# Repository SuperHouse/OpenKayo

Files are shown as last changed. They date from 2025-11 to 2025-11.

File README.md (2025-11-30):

# OpenKayo Kayo-A4 GCode Adapter

Connects to the serial interface of a Kayo-A4 pick-and-place
machine, and provides a USB interface with an onboard GCode 
interpreter that translates messages into the format necessary 
for the Kayo's motion controller.

This allows Kayo machines to be controlled using [OpenPnP](https://openpnp.org/).

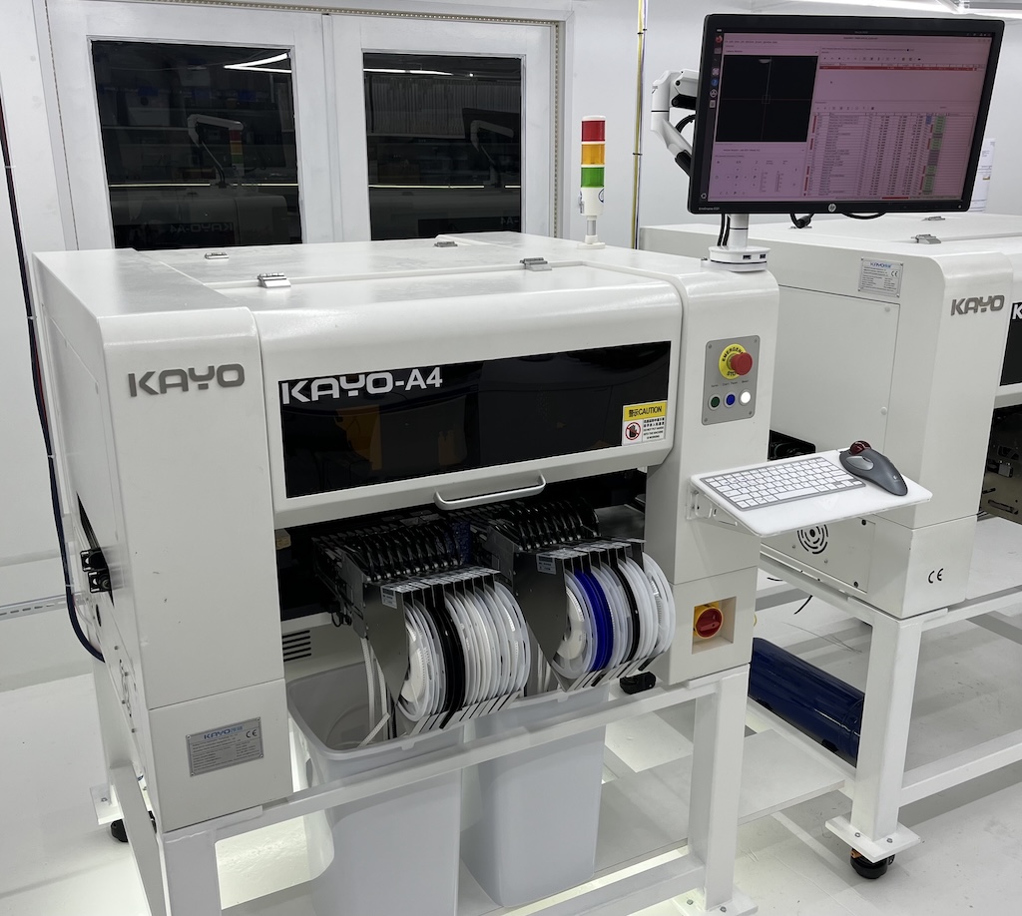
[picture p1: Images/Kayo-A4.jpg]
Kayo A4


## Hardware Requirements

You will need a computer running OpenPnP, with sufficient USB ports 
to handle the connections to the controller, cameras, etc. This 
is a normal OpenPnP requirement so check the OpenPnP docs for 
details.

The hardware adapter portion of the project can minimally be built with an
ESP8266-based dev board such as a Wemos D1 Mini and some cables.

A dedicated ESP32-S3 hardware design is provided, which includes
additional features such as a CAN bus interface to integrate with other
devices on the production line.

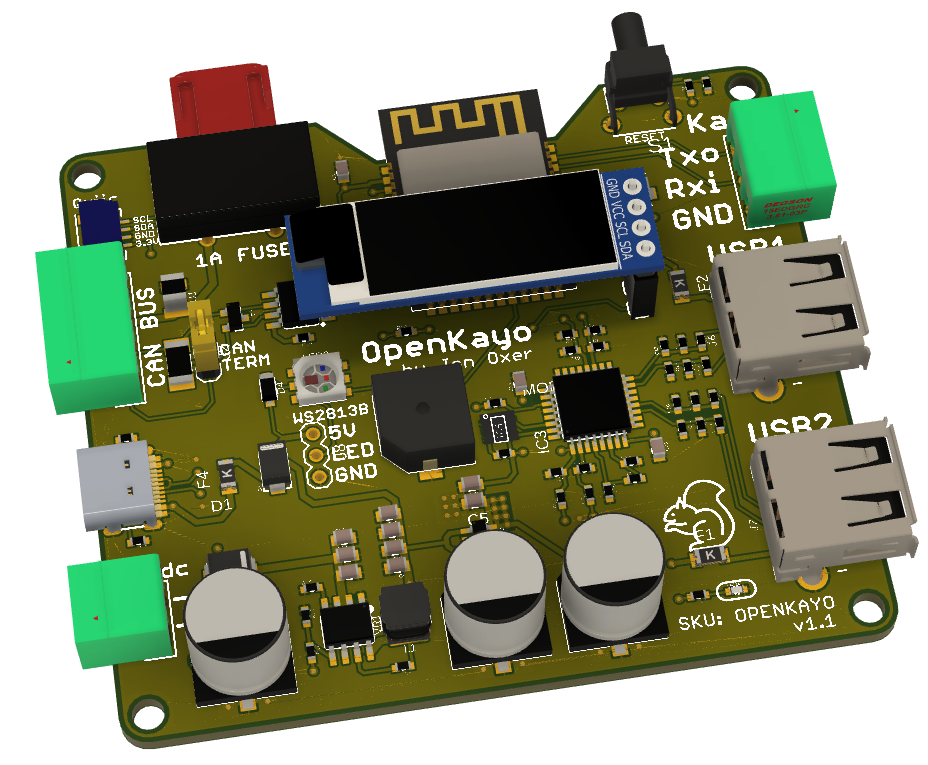
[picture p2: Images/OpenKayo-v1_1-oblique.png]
OpenKayo v1.1 interface board


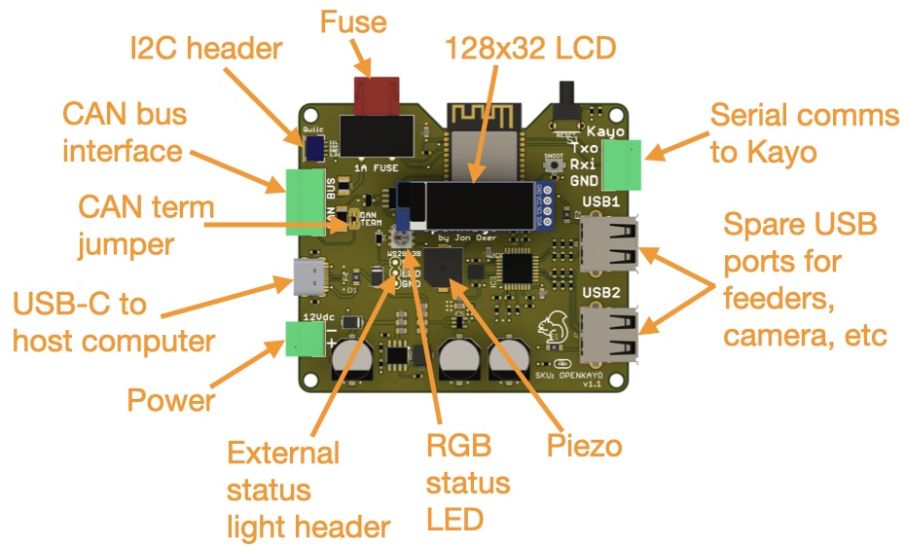
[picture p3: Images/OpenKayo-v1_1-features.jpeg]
OpenKayo v1.1 interface board features


**Adapter Board Features**

 * USB-C socket for connection to host computer running OpenPnP
 * ESP32-S3 MCU
 * 3-way 3.81mm screw socket for connection to Kayo serial cable
 * Onboard USB hub with 2 spare ports exposed
 * RGB LED for status display
 * Connections for external RGB LED strip for traffic-light status display etc
 * 128x32 OLED
 * Piezo for alarms
 * CAN bus interface with optional CAN termination
 * Can be powered via USB if only a serial connection + USB is required
 * Can be powered at 12V via screw terminals to pass power on to CAN bus
 * Can be powered at 12V via CAN bus if another device on the bus is powered

## Serial Connection

Kayo machines are supplied with a Windows PC running their proprietary 
control software, which is connected to a motion 
controller mounted inside the chassis via a serial connection. The
serial port is connected using a 3-way 3.81mm pitch pluggable screw 
terminal, which includes signal GND, TX, and RX:

 * Logic voltage: 3.3V
 * 115200 8N1

## Axis Configuration

The protocol converter uses the axes listed below. OpenPnP needs to be 
configured to use these same axes.

 * X: horizontal left/right
 * Y: horizontal forward/back
 * Z: virtual vertical axis for top camera, which doesn't physically move vertically
 * A, B, C, D: rotational axes for nozzles 1-4
 * I, J, K, L: z (vertical) axes for nozzles 1-4

Kayo "home" is in the top right corner at coordinates "0,0", so the 
working area is negative coordinates relative to that. That may sound 
confusing at first but it works out quite nicely in practice. For example, 
a typical board origin when clamped on the conveyor could be at something 
like "-155, -453".

Nozzles are at a 0 position when fully retracted (raised) and typically 
descend to approximately -9.8mm to -10.1mm to touch the surface of a clamped 
PCB or feeder pickup location.

## Supported G-Codes

### Basic movement

| Code | Meaning |
|---|---|
| G28 | Reset and home |
| G0 X*pos* Y*pos* | Move X & Y to the defined absolute position in mm, eg: "G0 X-23.4 Y-18" |
| G0 I*pos* | Move specified nozzle vertically to absolute position in mm, eg: "G0 I-7.6" to send nozzle 1 to -7.6mm (I=n1, J=n2, K=n3, L=n4) | 
| G0 A*pos* | Rotate specified nozzle to an absolute angle in degrees, eg: "G0 A48" to send nozzle 1 to an angle of 48 degrees (A=n1, B=n2, C=n3, D=n4) |

**Note:** the Kayo motion controller has an interlock on X/Y movement with Z 
axis displacement. You CANNOT move the machine in X or Y axis while holding 
a nozzle partly extended. It handles this by automatically retracting all 
nozzles whenever it gets an X/Y movement command.

This means that you can't use advanced motion planning in OpenPnP, and you 
also can't assume that you know the Z axis position of any nozzle. If you 
move the head in X/Y, all Z axes will be immediately zeroed with no warning.

### Vac / Blow
| Code | Meaning |
|---|---|
| M2 N*noz* | Close vac and open blow on specified nozzle, eg: "M2 N2" |
| M3 | Close vac and blow on all nozzles |
| M4 N*noz* | Open blow on selected nozzle, eg: "M4 N3" |
| M5 N*noz* | Close blow on selected nozzle, eg: "M5 N2" |
| M6 N*noz* | Open vac on selected nozzle, eg: "M6 N1" |
| M7 N*noz* | Close vac on selected nozzle, eg: "M7 N1" |

### Conveyor Belt
| Code | Meaning |
|---|---|
| M2 | Reset conveyor |
| M21 N*width* | Adjust conveyor to specified width + configured margin, eg: "M21 N93.4" |
| M22 | Ingest a PCB and clamp it in position |
| M23 | Unclamp PCB and move it to the exit location |
| M24 | Start conveyor |
| M25 | Stop conveyor and drop pin |
| M26 | Engages the stop pin |
| M27 | Clamp a PCB on the conveyor |

### Lights
| Code | Meaning |
|---|---|
| M30 | Turn off camera lights |
| M31 S*brightness* | Turn on fast camera light at specified brightness %, eg: "M31 S15" |
| M32 S*brightness* | Turn on precision camera light at specified brightness %, eg: "M32 S46" |

### Status
| Code | Meaning |
|---|---|
| M114 | Report position |
| M115 | Report firmware type and version |

### Feeders
| Code | Meaning |
|---|---|
| M600 N*feeder* | Open specified feeder, eg: "M600 N12" |
| M601 | Close feeders (no need to specify) |

**Note:** The Kayo motion controller only ever allows a single feeder to be open 
at a time. If you have one feeder open and then send an open command for a different 
feeder, the first one will be closed automatically.

There is no command to close a specific feeder. M601 closes whatever was last opened.

### Diagnostic
| Code | Meaning |
|---|---|
|M99 N*noz* S*steps* | Send microsteps to specified nozzle rotation stepper, eg: "M99 N1 S1234" |

## Camera Modifications

### Bottom Cameras

I have been unable to connect the 5 factory bottom cameras (1 x precision 
camera and a 4-way high-speed camera array) to OpenPnP on either 
Ubuntu or MacOS. You may have more success on Windows: please let me know!

On my machines I have unscrewed the 4-way camera array and tucked it away 
under the feeder manifold, and also removed the precision camera. I replaced 
that with an ELP Mini 720p OV9712 USB industrial camera with a 6mm lens, 
using a 3D-printed camera mount and a lens spacer to change the focal length.

This particular camera is very commonly used for OpenPnP so it's a 
well-known and well-supported device.

**1. Remove light bracket and the original camera:**

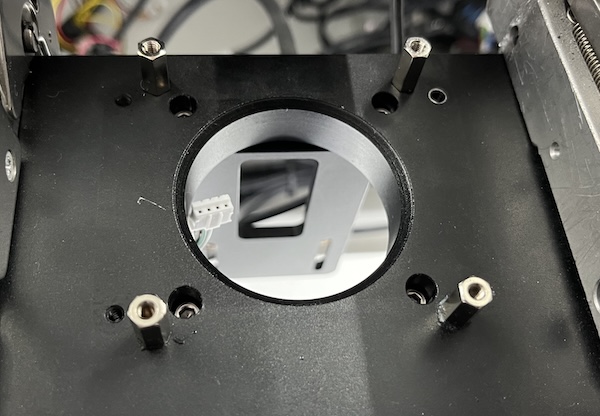
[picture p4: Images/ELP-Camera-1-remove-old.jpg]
Remove original camera


**2. 3D-print mounting plate and lens spacer:**

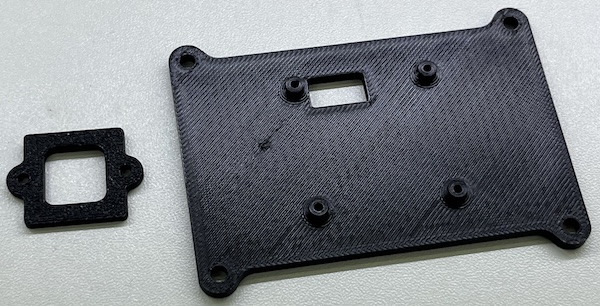
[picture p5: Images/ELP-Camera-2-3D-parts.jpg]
3D printed parts


**3. Remove lens from ELP camera:**

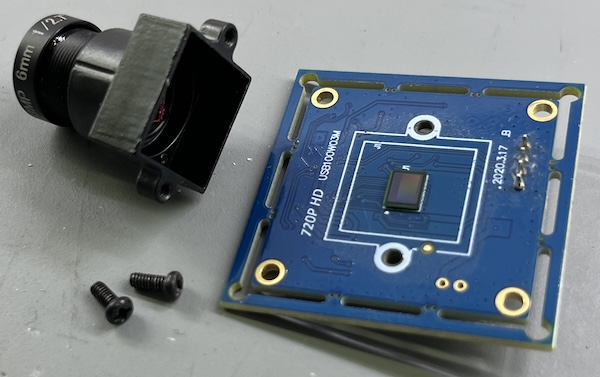
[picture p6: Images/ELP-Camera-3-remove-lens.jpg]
Remove ELP lens


**4. Reattach lens with 6mm M2 bolts with spacer:**

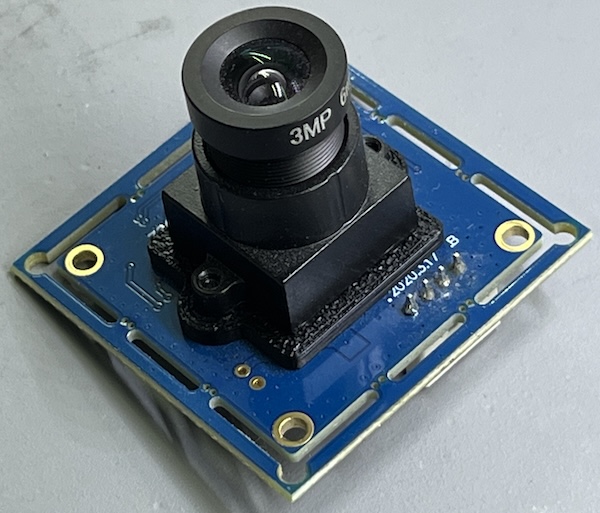
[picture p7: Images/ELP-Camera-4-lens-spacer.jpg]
Lens spacer


**5. Attach mounting plate with M3 bolts:**

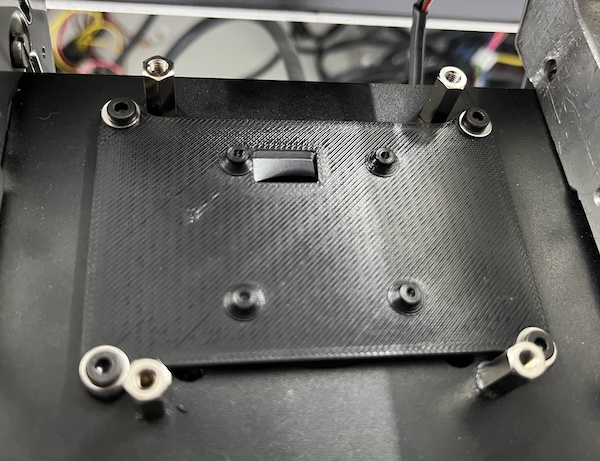
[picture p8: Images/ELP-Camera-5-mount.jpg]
Attach mount Attach mounting plate


**6. Pass cable through mounting plate and screw camera on with 2mm self tappers:**

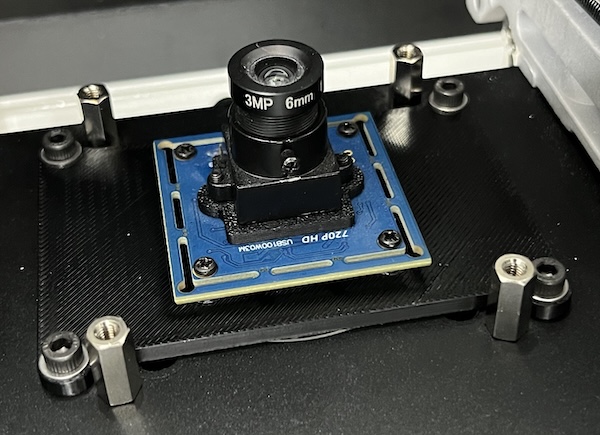
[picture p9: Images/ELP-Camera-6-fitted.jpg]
Fitted camera


Finally, reinstall the light bracket and then do the usual focus and 
camera calibration process in OpenPnP.

### Top Camera

The top camera has an analog output. I connected it to an analog-to-HDMI 
converter, which then goes to a cheap HDMI-to-USB converter so that it 
appears as a webcam under Linux and can be accessed by OpenPnP.

## Discard Tray

You can use the original discard tray behind the PCB area, but with 
the 4-camera array removed there is an ideal location for a discard 
tray right behind the camera location. This allows a very short movement 
to the tray if the vision pipeline rejects the parts.

I have designed a discard tray holder that has a 1x2 Gridfinity mount 
in the base, and holes to attach it to the T-slot front rail using 
T-nuts and M3 bolts:

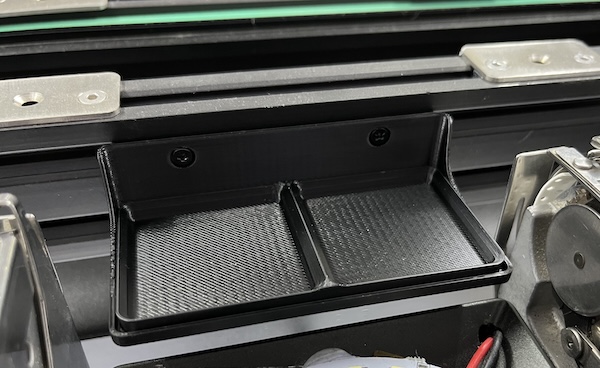
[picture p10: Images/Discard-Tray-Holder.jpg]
Discard tray holder


You can use a regular 1x2 Gridfinity tray. I've included a design for 
a 1x1 tray with the height set to match the mounting rail. OpenPnP 
currently only supports a single discard location, but support for 
multiple trays is in development:

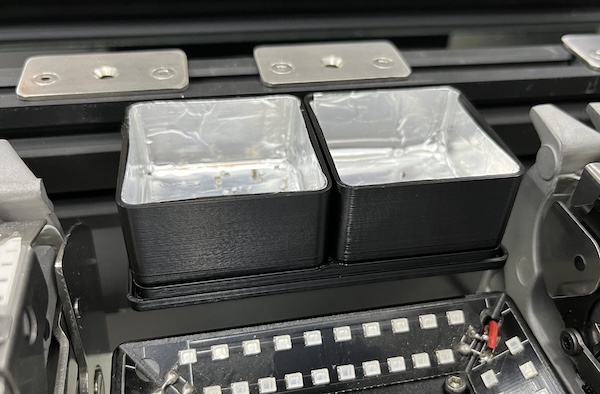
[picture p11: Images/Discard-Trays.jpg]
Discard trays


## Kayo Protocol

The control protocol for the Kayo motion controller uses 8-byte 
messages in both directions, with no terminator. Message boundaries 
are discovered by watching for a leading character, tracking the 
number of bytes received, and timing out as a fallback to handle 
incomplete messages or errors.

The protocol is embodied in the source code. Docs to be added here 
later.

## Hardware

The "Hardware" directory contains the PCB design as an EAGLE project. 
This can be imported into KiCAD, or opened natively using Fusion360.

## Firmware

The "Firmware" directory contains example firmware as an Arduino
project.

## Credits

 * Jonathan Oxer <jon@oxer.com.au>

Heavily inspired by Glen English's Python-based UI for the Kayo, in
particular his work decoding the message format used by the factory
software.

## License

Copyright 2022-2025 SuperHouse Automation Pty Ltd  www.superhouse.tv  

The hardware portion of this project is licensed under the TAPR Open
Hardware License (www.tapr.org/OHL). The "license" folder within this
repository contains a copy of this license in plain text format.

The software portion of this project is licensed under the Simplified
BSD License. The "licence" folder within this project contains a
copy of this license in plain text format.

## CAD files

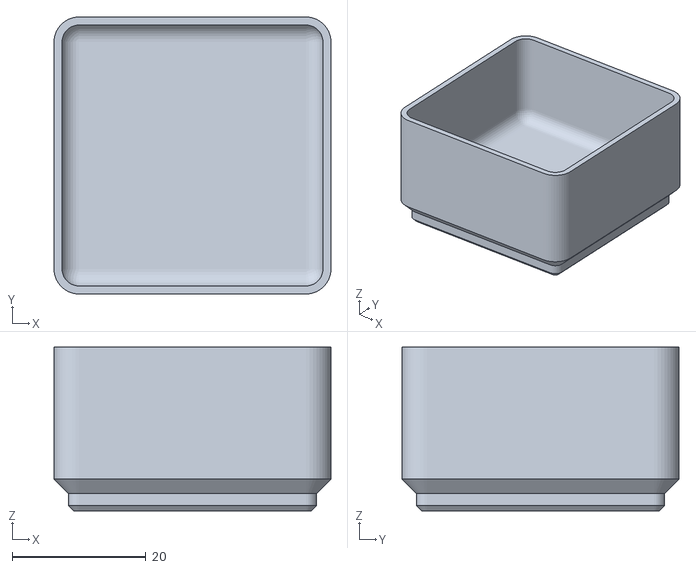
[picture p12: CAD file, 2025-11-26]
Mechanical/Discard Tray Gridfinity 1x1 z=3.5.stl
41.5 x 41.5 x 24.5

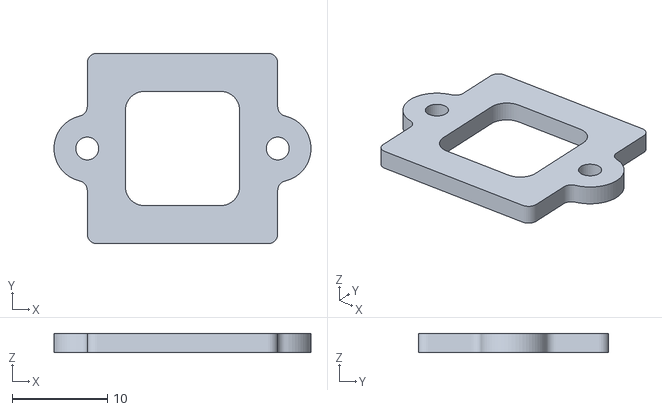
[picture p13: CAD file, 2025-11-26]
Mechanical/ELP Camera Lens Spacer.stl
27.0 x 20.0 x 2.00

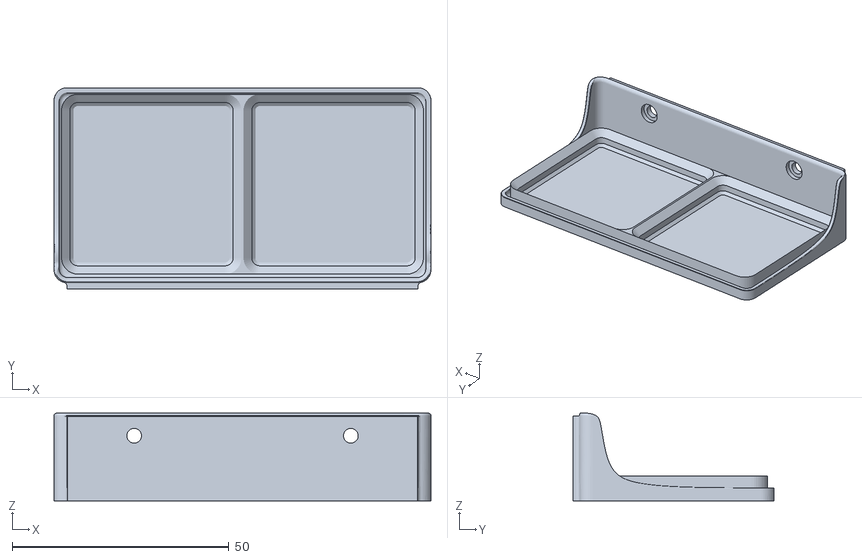
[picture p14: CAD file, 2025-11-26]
Mechanical/Discard Tray Holder Gridfinity.stl
87.0 x 46.5 x 20.2

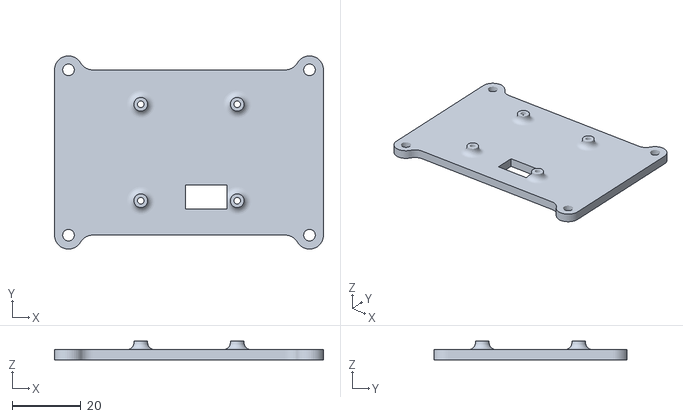
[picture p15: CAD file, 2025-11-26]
Mechanical/ELP Camera Mount Topside.stl
78.1 x 56.1 x 5.50

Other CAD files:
Mechanical/Discard Tray Gridfinity 1x1 z=3.5.f3d
Mechanical/Discard Tray Holder Gridfinity.f3d
Mechanical/ELP Camera Lens Spacer.f3d
Mechanical/ELP Camera Mount Topside.f3d

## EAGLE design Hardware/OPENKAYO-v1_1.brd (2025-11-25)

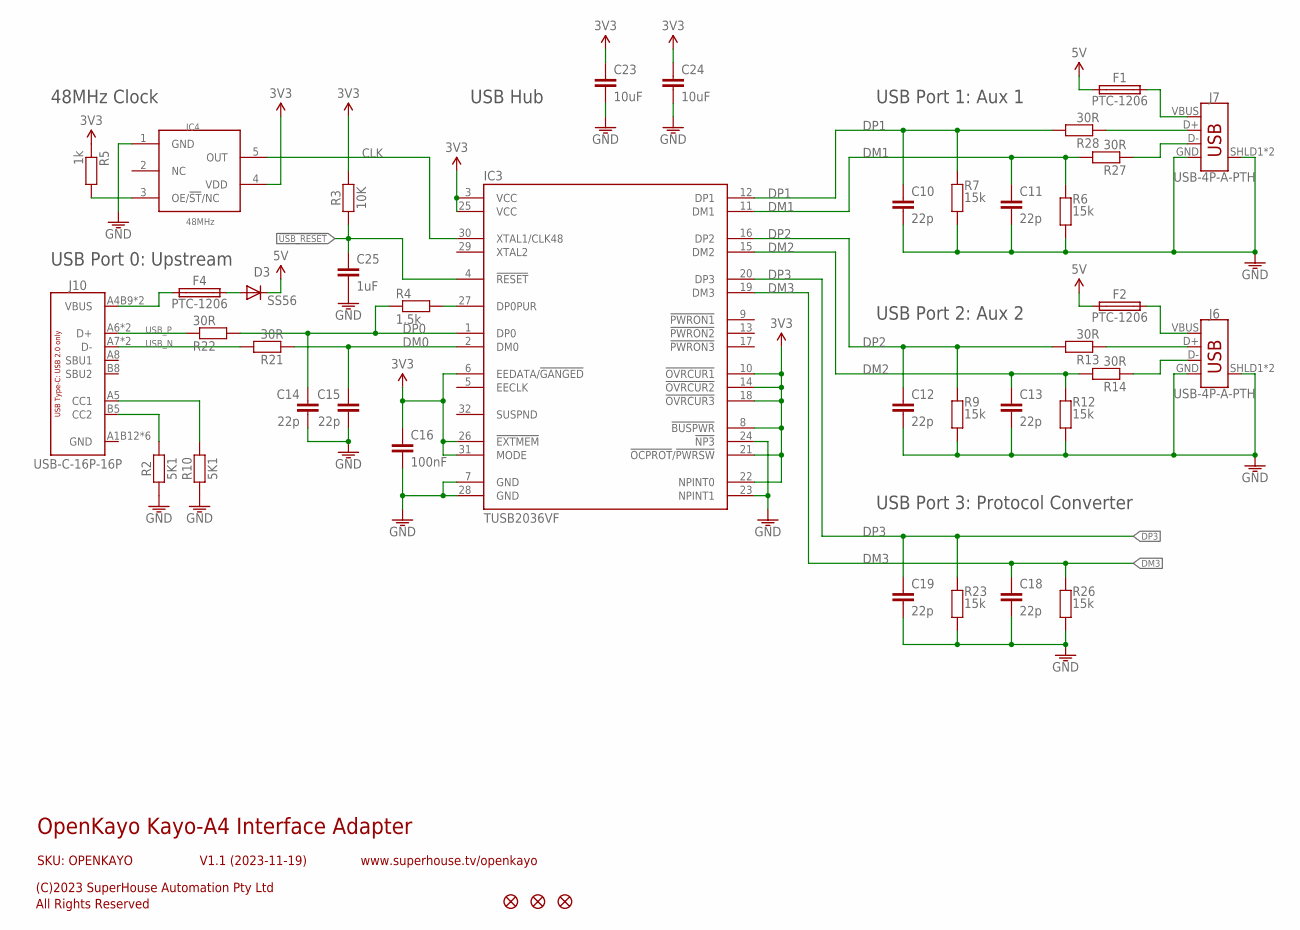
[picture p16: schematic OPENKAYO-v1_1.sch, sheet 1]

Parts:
C10, C11, C12, C13, C14, C15, C18, C19: 22p; C0603
C16: 100nF; C0603
C23, C24: 10uF; C0805
C25: 1uF; C0603
D3: SS56; SMA-DIODE
F1, F2, F4: PTC-1206; 1206
FID1, FID2, FID3: FIDUCIAL1X2.5; FIDUCIAL-1X2.5
IC3: TUSB2036VF; PQFP-G32
IC4: 48MHz; SOT-23-5
J6, J7: USB-4P-A-PTH; USB-A-PTH
J10: USB-C-16P-16P; USB-C-16P
R2, R10: 5K1; R0603
R3: 10K; R0603
R4: 1.5k; R0603
R5: 1k; R0603
R6, R7, R9, R12, R23, R26: 15k; R0603
R13, R14, R21, R22, R27, R28: 30R; R0603

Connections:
3.3V: C16.1, C23.1, C24.1, IC3.3 (VCC), IC3.6 (EEDATA/!GANGED), IC3.8 (!BUSPWR), IC3.10 (!OVRCUR1), IC3.14 (!OVRCUR2), IC3.18 (!OVRCUR3), IC3.21 (!OCPROT!/!PWRSW!), IC3.22 (NPINT0), IC3.25 (VCC), IC3.26 (!EXTMEM), IC3.31 (MODE), IC4.4 (VDD), R3.2, R5.1; also elsewhere on the board
5V: D3.C, F1.1, F2.1; also elsewhere on the board
!USB_RESET: C25.1, IC3.4 (!RESET), R3.1
CLK: IC3.30 (XTAL1/CLK48), IC4.5 (OUT)
DM0: C15.1, IC3.2 (DM0), R21.2
DM1: C11.1, IC3.11 (DM1), R6.1, R27.2
DM2: C13.1, IC3.15 (DM2), R12.1, R14.2
DM3: C18.1, IC3.19 (DM3), R26.1; also elsewhere on the board
DP0: C14.1, IC3.1 (DP0), R4.1, R22.2
DP1: C10.1, IC3.12 (DP1), R7.1, R28.2
DP2: C12.1, IC3.16 (DP2), R9.1, R13.2
DP3: C19.1, IC3.20 (DP3), R23.1; also elsewhere on the board
GND: C10.2, C11.2, C12.2, C13.2, C14.2, C15.2, C16.2, C18.2, C19.2, C23.2, C24.2, C25.2, IC3.7 (GND), IC3.23 (NPINT1), IC3.24 (!NP3), IC3.28 (GND), IC4.1 (GND), J6.GND, J6.SHLD1 (SHIELD), J6.SHLD2 (SHIELD), J7.GND, J7.SHLD1 (SHIELD), J7.SHLD2 (SHIELD), J10.A1B12 (GND), J10.A12B1 (GND), J10.FIX1 (GND), J10.FIX2 (GND), J10.FIX3 (GND), J10.FIX4 (GND), R2.1, R6.2, R7.2, R9.2, R10.1, R12.2, R23.2, R26.2; also elsewhere on the board
unnamed: IC3.27 (DP0PUR), R4.2
unnamed: IC4.3 (OE/!ST!/NC), R5.2
unnamed: F1.2, J7.VBUS
unnamed: F2.2, J6.VBUS
unnamed: J10.B5 (CC2), R2.2
unnamed: J10.A5 (CC1), R10.2
unnamed: J6.D+, R13.1
unnamed: J6.D-, R14.1
unnamed: J7.D+, R28.1
unnamed: J7.D-, R27.1
unnamed: F4.1, J10.A4B9 (VBUS), J10.A9B4 (VBUS)
unnamed: D3.A, F4.2
USB_N: J10.A7 (D-), J10.B7 (D-), R21.1
USB_P: J10.A6 (D+), J10.B6 (D+), R22.1

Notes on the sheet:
OpenKayo Kayo-A4 Interface Adapter
V1.1 (2023-11-19)
SKU: OPENKAYO
(C)2023 SuperHouse Automation Pty Ltd
All Rights Reserved
www.superhouse.tv/openkayo
USB Port 1: Aux 1
USB Port 2: Aux 2
USB Port 3: Protocol Converter
USB Hub
USB Port 0: Upstream
48MHz Clock

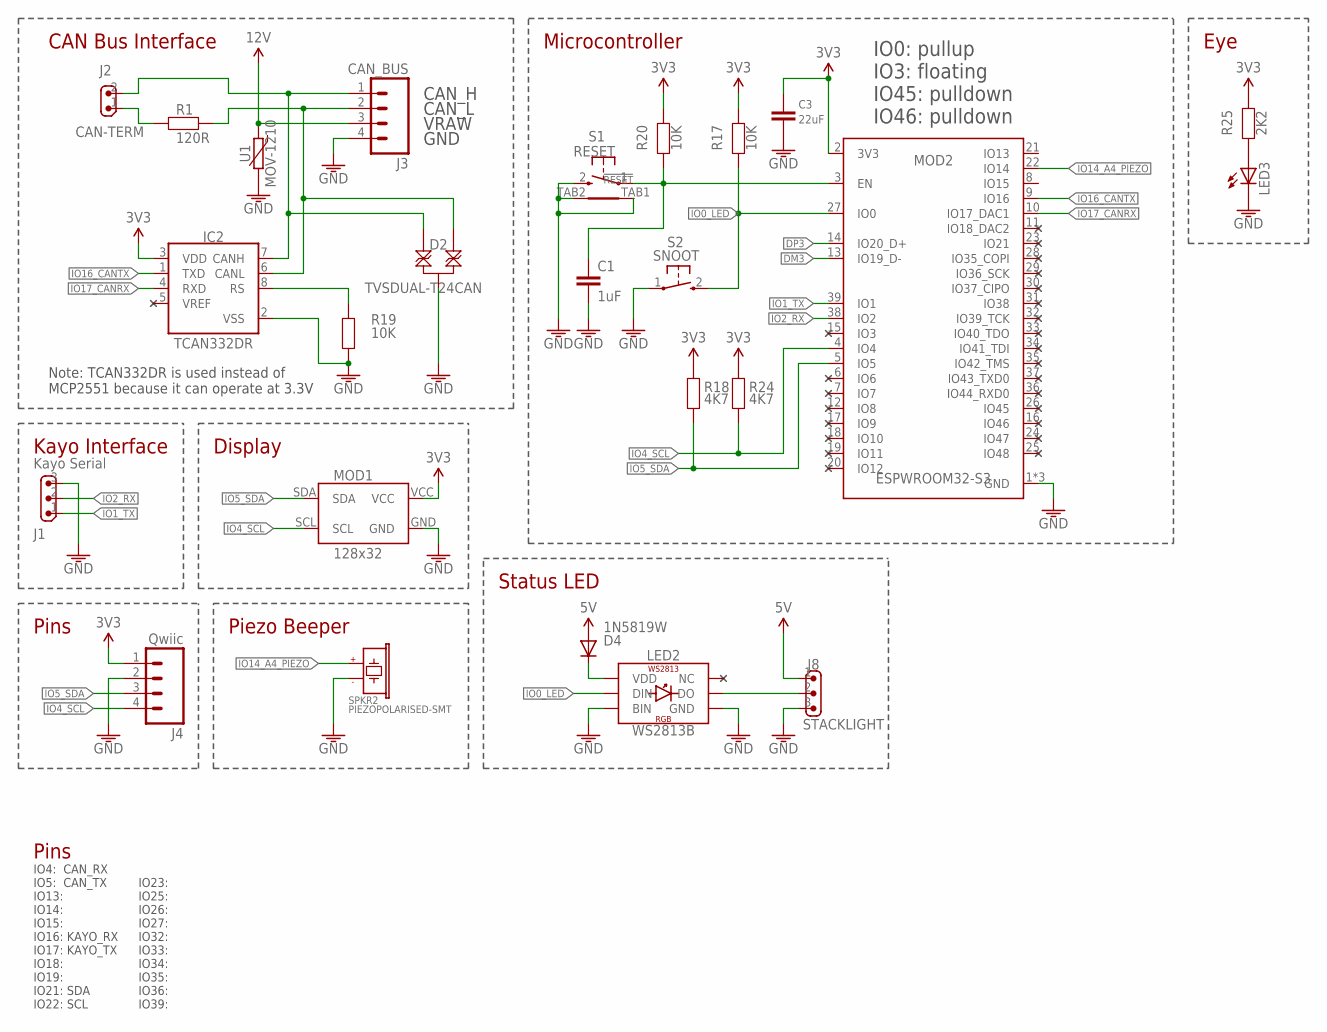
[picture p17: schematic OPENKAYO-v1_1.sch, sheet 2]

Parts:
C1: 1uF; C0603
C3: 22uF; C0805
D2: TVSDUAL-T24CAN; SOT23-3
D4: 1N5819W; SOD-123
IC2: TCAN332DR; SOIC8
J1: Kayo Serial; SCREWTERMINAL-3.81MM-HOR-3
J2: CAN-TERM; 1X02-P-JUMP-Y
J3: CAN_BUS; SCREWTERMINAL-3.81MM-HOR-4
J4: Qwiic; JST-SM4B-SH
J8: STACKLIGHT; 1X03
LED2: WS2813B; WS2813
LED3: LED0603; LED-0603
MOD1: 128x32; OLED-128X32-0.91-HEADER
MOD2: ESPWROOM32-S3
R1: 120R; R2010
R17, R19, R20: 10K; R0603
R18, R24: 4K7; R0603
R25: 2K2; R0603
S1: RESET; TYCO-FSMRAJ
S2: SNOOT; TACTILE_SMT_3X4X2
SPKR2: PIEZOPOLARISED-SMT; PIEZO-9.6X9.6-SMT
U1: MOV-1210; 1210

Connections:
3.3V: C3.1, IC2.3 (VDD), J4.1, MOD1.VCC, MOD2.2 (3V3), R17.1, R18.1, R20.1, R24.1, R25.1; also elsewhere on the board
5V: D4.2 (A), J8.1; also elsewhere on the board
12V: J3.3, U1.2; also elsewhere on the board
!RESET: C1.1, MOD2.3 (EN), R20.2, S1.1
CAN_H: D2.2, IC2.7 (CANH), J2.2, J3.1
CAN_L: D2.1, IC2.6 (CANL), J3.2, R1.2
DM3: MOD2.13 (IO19_D-); also elsewhere on the board
DP3: MOD2.14 (IO20_D+); also elsewhere on the board
GND: C1.2, C3.2, D2.3, IC2.2 (VSS), J1.3, J3.4, J4.2, J8.3, LED2.5 (GND), LED2.6 (BIN), LED3.C, MOD1.GND, MOD2.1 (GND), MOD2.40 (GND), MOD2.41 (GND), R19.1, S1.2, S1.TAB1, S1.TAB2, S2.1, SPKR2.2 (-), U1.1; also elsewhere on the board
IO0_LED: LED2.4 (DIN), MOD2.27 (IO0), R17.2, S2.2 (S)
IO1_TX: J1.1, MOD2.39 (IO1)
IO2_RX: J1.2, MOD2.38 (IO2)
IO4_SCL: J4.4, MOD1.SCL, MOD2.4 (IO4), R24.2
IO5_SDA: J4.3, MOD1.SDA, MOD2.5 (IO5), R18.2
IO14_A4_PIEZO: MOD2.22 (IO14), SPKR2.1 (+)
IO16_CANTX: IC2.1 (TXD), MOD2.9 (IO16)
IO17_CANRX: IC2.4 (RXD), MOD2.10 (IO17_DAC1)
IO46: MOD2.16 (IO46)
unnamed: IC2.8 (RS), R19.2
unnamed: LED3.A, R25.2
unnamed: J2.1, R1.1
unnamed: D4.1 (C), LED2.2 (VDD)
unnamed: J8.2, LED2.3 (DO)
NC: LED2.1 (NC)

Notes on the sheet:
CAN Bus Interface
Note: TCAN332DR is used instead of MCP2551 because it can operate at 3.3V
CAN_H
CAN_L
GND
VRAW
Kayo Interface
Piezo Beeper
IO4: CAN_RX IO5: CAN_TX IO13: IO14: IO15: IO16: KAYO_RX IO17: KAYO_TX IO18: IO19: IO21: SDA IO22: SCL
Pins
IO23: IO25: IO26: IO27: IO32: IO33: IO34: IO35: IO36: IO39:
Microcontroller
Display
Status LED
IO0: pullup IO3: floating IO45: pulldown IO46: pulldown
Eye

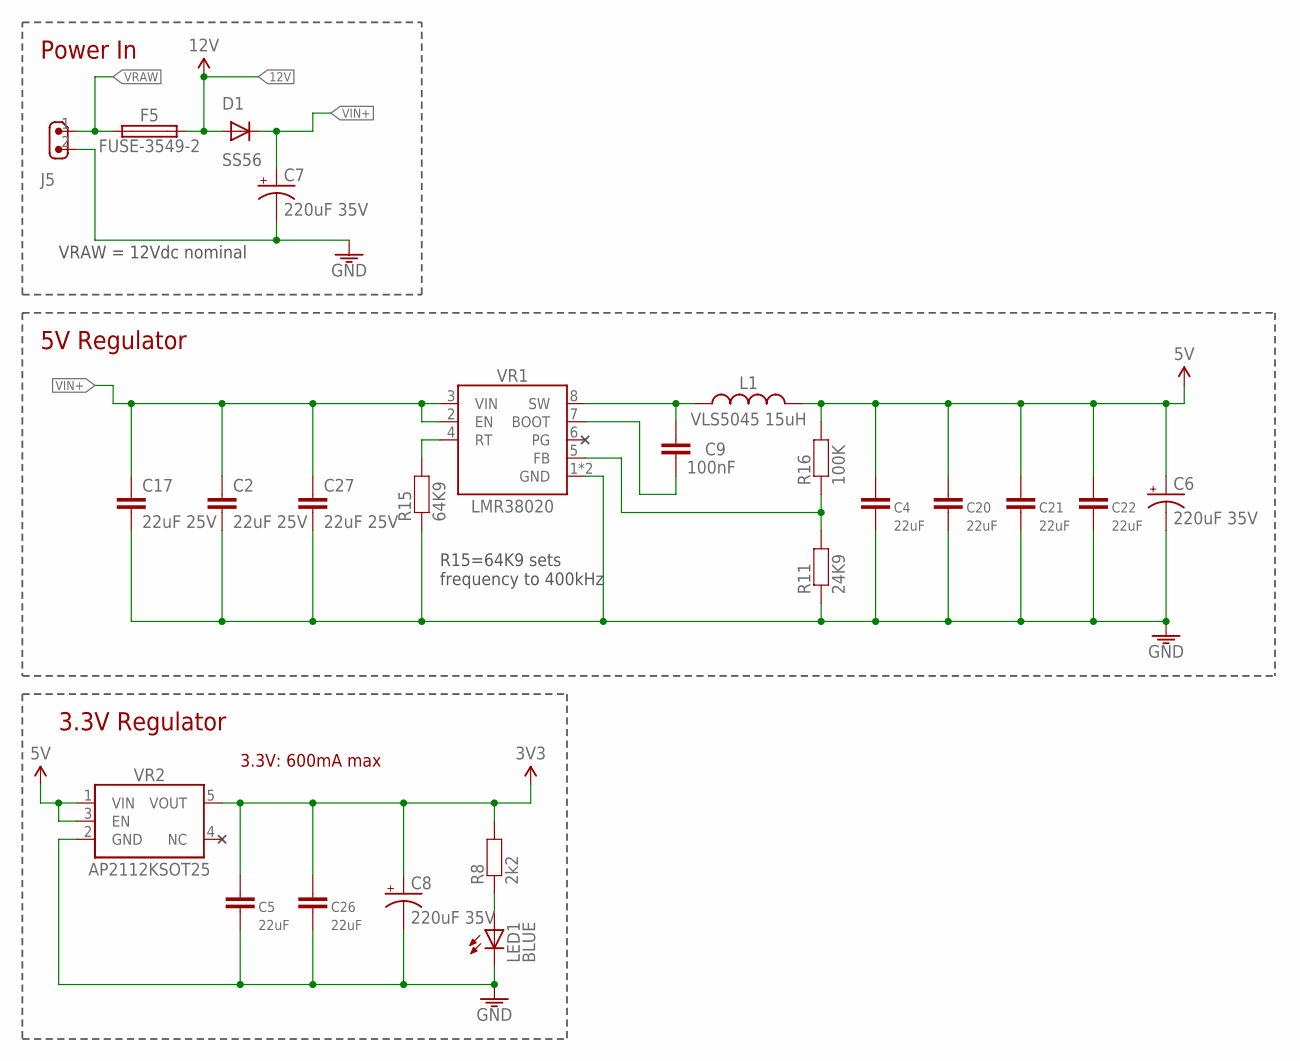
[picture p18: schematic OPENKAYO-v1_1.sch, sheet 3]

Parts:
C2, C17, C27: 22uF 25V; C0805
C4, C5, C20, C21, C22, C26: 22uF; C0805
C6, C7, C8: 220uF 35V; PANASONIC_G
C9: 100nF; C0603
D1: SS56; SMA-DIODE
F5: FUSE-3549-2; KS-3549-2
J5: M02-SCREW-3.81MM-HOR; SCREWTERMINAL-3.81MM-HOR-2
L1: VLS5045 15uH; INDUCTOR-5045
LED1: BLUE; LED-0603
R8: 2k2; R0603
R11: 24K9; R0603
R15: 64K9; R0603
R16: 100K; R0603
VR1: LMR38020; HSOIC8
VR2: AP2112KSOT25; SOT23-5

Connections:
3.3V: C5.1, C8.+, C26.1, R8.2, VR2.5 (VOUT); also elsewhere on the board
5V: C4.1, C6.+, C20.1, C21.1, C22.1, L1.2, R16.2, VR2.1 (VIN), VR2.3 (EN); also elsewhere on the board
12V: D1.A, F5.3 (2), F5.4 (2); also elsewhere on the board
GND: C2.2, C4.2, C5.2, C6.-, C7.-, C8.-, C17.2, C20.2, C21.2, C22.2, C26.2, C27.2, J5.2, LED1.C, R11.1, R15.1, VR1.1 (GND), VR1.TGND (GND), VR2.2 (GND); also elsewhere on the board
unnamed: C9.1, L1.1, VR1.8 (SW)
unnamed: R15.2, VR1.4 (RT)
unnamed: R11.2, R16.1, VR1.5 (FB)
unnamed: C9.2, VR1.7 (BOOT)
unnamed: LED1.A, R8.1
PG: VR1.6 (PG)
VIN+: C2.1, C7.+, C17.1, C27.1, D1.C, VR1.2 (EN), VR1.3 (VIN)
VRAW: F5.1, F5.2 (1), J5.1

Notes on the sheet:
3.3V: 600mA max
VRAW = 12Vdc nominal
5V Regulator
3.3V Regulator
Power In
R15=64K9 sets frequency to 400kHz

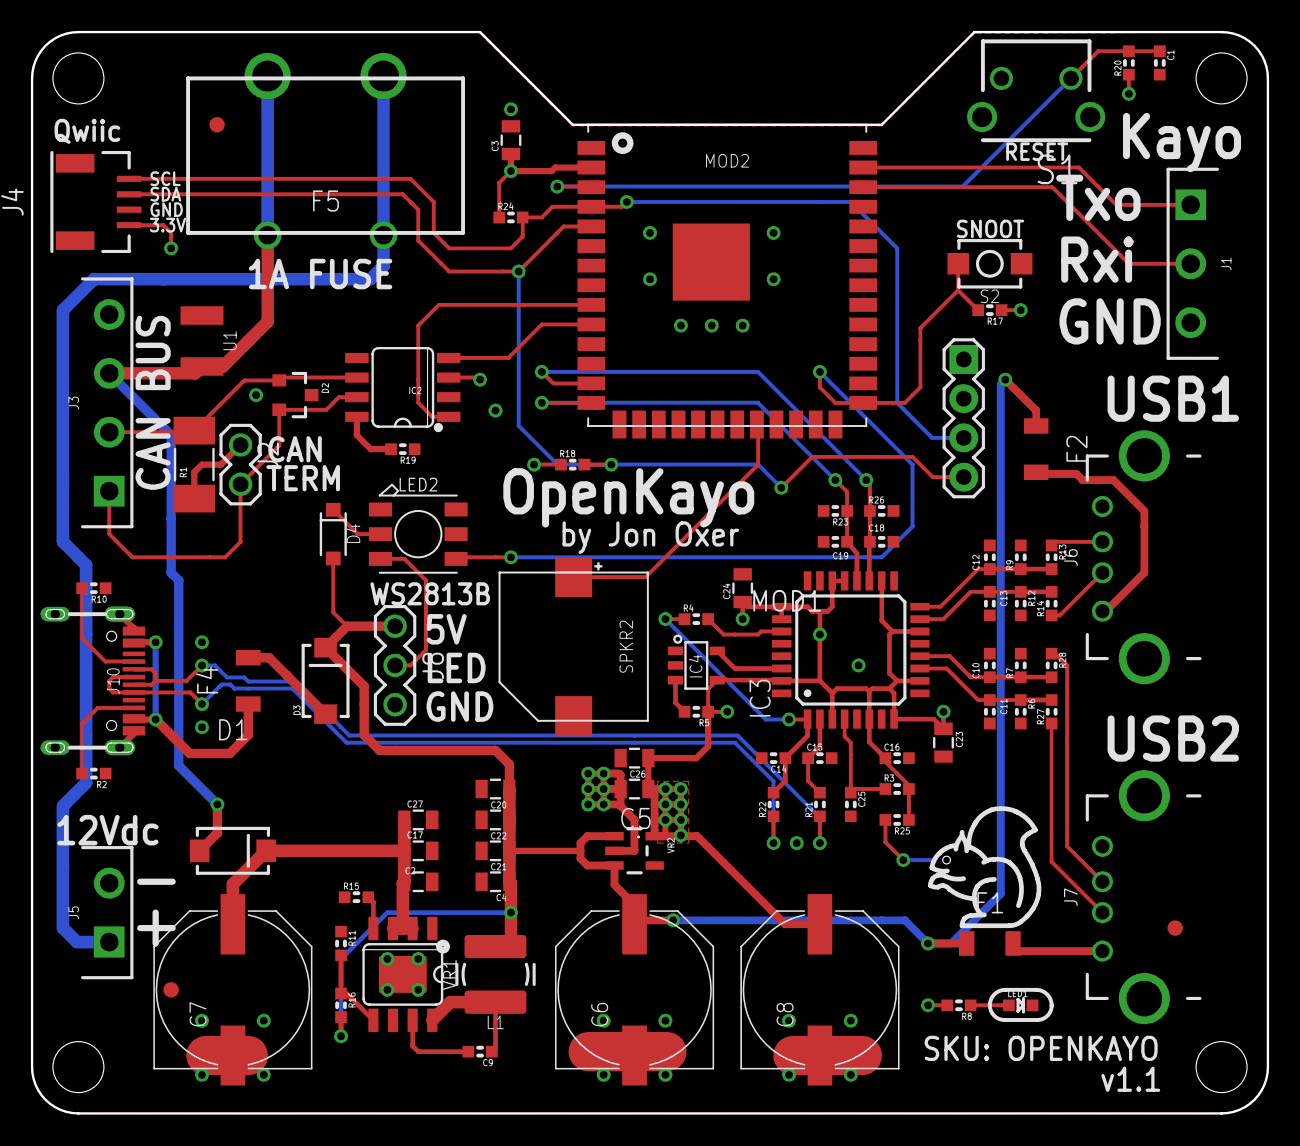
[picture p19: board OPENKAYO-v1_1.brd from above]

Board: 4 copper layers, 80.0 x 70.0 mm, 90 parts (1 on the bottom side), 51 nets.

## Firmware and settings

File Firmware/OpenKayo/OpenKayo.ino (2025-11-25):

/*
  Kayo-A4 Pick-and-Place GCode Interface Firmware

  Written by Jonathan Oxer <jon@oxer.com.au>

  Inspired by a Python-based Kayo control system written by Glen English.

  Controlled using GCODE. Understands these codes:

  === Basic movement ===
  "G28"             Reset and home
  "G0 X-23.4 Y-18"  Move X & Y to the defined absolute position
  "G0 I-8.9"        Move nozzle 1 vertically      (I=1, J=2, K=3, L=4)
  "G0 A48"          Rotate nozzle 1 to 48 degrees (A=1, B=2, C=3, D=4)

  === Vac / Blow ===
  "M2 N2"           Close vac and open blow on nozzle 2
  "M3"              Close vac and blow on all nozzles
  "M4 N2"           Open blow on nozzle 2
  "M5 N1"           Close blow on nozzle 1
  "M6 N3"           Open vac on nozzle 3
  "M7 N3"           Close vac on nozzle 3

  === Conveyor Belt ===
  "M20"             Reset conveyor
  "M21 N93.4"       Adjust conveyor to 93.4mm width + margin
  "M22"             Ingest a PCB and clip it in position
  "M23"             Unclip PCB and move it to the exit location
  "M24"             Start conveyor
  "M25"             Stop conveyor and drop pin
  "M26"             Engages the stop pin
  "M27"             Clip a PCB on the conveyor

  === Lights ===
  "M30"             Turn off camera lights
  "M31 S15"         Turn on fast camera light at 15% brightness
  "M32 S46"         Turn on precision camera light at 46% brightness

  === Status ===
  "M114"            Report position
  "M115"            Report firmware type and version

  === Feeders ===
  "M600 N12"        Open feeder 12
  "M601"            Close feeders (no need to specify)

  === Diagnostic ===
  "M99 N1 S1234"    Send 1234 microsteps to N1


  X axis is horizontal left/right.
  Y axis is horizontal forward/back.
  Kayo home is top right corner, so the working area is negative coordinates
  relative to that.

  What to do about Z axis? Just 1 Z, or a separate Z for each nozzle? I/J/K/L?
  A-D are the axes used for rotation of nozzles 1-4.
  Ideally this firmware should support 8-nozzle machines, so allowing for
  8 x Z axes and 8 x rotation axes is best.

  No movement is allowed until the home sequence has been completed.

  Arduino IDE ESP32 board profile:
  Go into Preferences -> Additional Board Manager URLs
  Add:
   https://dl.espressif.com/dl/package_esp32_index.json

  Then go to Tools -> Board -> Boards Manager..., update, and add "esp32 by Espressif Systems"

  Arduino IDE settings under "Tools":
    - Board:            ESP32-S3 Dev Module
    - Upload speed:     115200bps
    - CPU Speed:        240MHz
    - Flash Frequency:  40MHz
    - Flash Mode:       DOUT
    - Flash Size:       4MB
    - Partition Scheme: Minimal SPIFFS (1.9MB APP with OTA/190KB SPIFFS)
    - Core Debug Level: None
    - PSRAM:            Disabled

  To do:
    - Fix interaction between XY and Z axis movements.
    - Query machine for position report instead of using stored position.
    - Make received message parser resilient to missed characters.
    - Figure out why machines have different microstep counts on Z axis.
*/
#define VERSION "0.3-20230721"


/*--------------------------- Configuration ---------------------------------*/
// Configuration should be done in the included file:
#include "config.h"

/*--------------------------- Libraries -------------------------------------*/
#include "driver/twai.h"                      // For CAN bus
#include "Wire.h"

/*--------------------------- Global Variables ------------------------------*/
uint8_t  g_homed                 = false;
uint8_t  g_kayo_send_buffer[8]   = {0x00, 0x00, 0x00, 0x00, 0x00, 0x00, 0x00, 0x00};
uint8_t  g_kayo_recv_buffer[8]   = {0x00, 0x00, 0x00, 0x00, 0x00, 0x00, 0x00, 0x00};
uint8_t  g_expected_response[8]  = {0xAA, 0x00, 0x00, 0x00, 0x00, 0x00, 0x00, 0x55};
//uint8_t  g_recv_buffer_position  = 0;
float    g_x_position            = 0.0;
float    g_y_position            = 0.0;
float    g_nozzle_angle[4]       = {0.0, 0.0, 0.0, 0.0};
float    g_nozzle_z_position[4]  = {0.0, 0.0, 0.0, 0.0};
uint8_t  g_matching_response     = false;
float    g_x_reported_position   = 0.0;
float    g_y_reported_position   = 0.0;

// g_position_message is maintained as a global, populated with the latest requested
// position values. This allows persistence of values that haven't been requested in
// a specific move. For example, "G0 X123" will move to 123,0. Then a subsequent
// "G0 Y321" would move to 123,321 because the previous X value is persisted.
uint8_t  g_position_message[8]   = {0xAA, 0x00, 0x00, 0x00, 0x00, 0x00, 0x00, 0x55};

#define  MAX_USB_INPUT             80 // Input buffer size

// General
uint64_t g_device_id;                 // Unique ID from ESP chip ID

// CAN bus
uint16_t g_can_source_address    = J1939_SOURCE_ADDRESS; // Set statically
uint32_t g_last_can_rx_time      = 0;      // ms when last message was received
uint32_t g_last_can_tx_time      = 0;      // ms when last message was sent


/*--------------------------- Function Signatures ---------------------------*/
void sendMessageToKayo(uint8_t message[8], bool suppress_ok_response = false, bool exact_response_required = false);
void decodePositionMessage(uint8_t message[]);
void cmdResetAndHome();
void cmdMoveXY(float x, float y, bool suppress_ok_response = false);
void cmdMoveZ(uint8_t n, float z, bool suppress_ok_response = false);
void cmdRotateNozzle(uint8_t n, float a);

void cmdSetVacBlow(uint16_t command_code, uint8_t nozzle_id);
void openSupplimentValve();
void closeSupplimentValve();

void cmdResetConveyor();
void cmdAdjustConveyorWidth(float width_requested);
void cmdRunConveyor();
void cmdStopConveyor();
void cmdStopPinEngageConveyor();
void cmdClipPcbConveyor();
void cmdExitPcbConveyor();
void cmdIngestPcbManual();
void cmdIngestPcbConveyor();

void cmdLightOn(uint8_t light, uint8_t brightness);
void cmdLightsOff();

void cmdReportPosition();

void cmdOpenFeeder(uint8_t feeder_id);
void cmdCloseFeeders();

void printKayoMessage(uint8_t message[]);
void listenToKayoSerialStream(bool suppress_ok_response = false, bool exact_match_required = false);
void clearExpectedResponse();
//void addMessageToQueue(uint8_t message[], uint8_t expected_response[]);

void cmdSendZSteps(uint8_t n, uint16_t z_microsteps);

void sendConveyorWidthToCAN(uint16_t requested_width);
void sendHomeToCAN();

/*--------------------------- Instantiate Global Objects --------------------*/


/*--------------------------- Program ---------------------------------------*/
/* Resources */
#include "gcode.h"
#include "serial_comms.h"
#include "can_comms.h"
#include "machine_actions.h"

/*
  Setup
*/
void setup()
{
  Wire.begin(I2C_SDA_PIN, I2C_SCL_PIN);
  Serial.begin(SERIAL_BAUD_RATE);
  while (!Serial)
  {
    // nothing
  }
  Serial.print("OpenKayo GCode adapter v");
  Serial.println(VERSION);

  // We need a unique device ID
  g_device_id = ESP.getEfuseMac();
  Serial.print("Device ID: ");
  Serial.println(g_device_id, HEX);

  if (ENABLE_KAYO) {
    //Serial2.begin(KAYO_BAUD_RATE, SERIAL_8N1, KAYO_TX_PIN, KAYO_RX_PIN); // <-- Rack32
    Serial2.begin(KAYO_BAUD_RATE, SERIAL_8N1, KAYO_RX_PIN, KAYO_TX_PIN);
  }

  g_usb_input_buffer.reserve(MAX_USB_INPUT);

  /* Set up the CAN interface */
  //  if (ESP.getChipRevision() >= 2)
  //  {
  //    if (!CAN.begin(CAN_BUS_SPEED * 2))
  //    {
  //      Serial.println("CAN failed!");
  //    } else {
  //      Serial.println("CAN initialised");
  //    }
  //  } else {
  //    if (!CAN.begin(CAN_BUS_SPEED))
  //    {
  //      Serial.println("CAN failed!");
  //    } else {
  //      Serial.println("CAN initialised");
  //    }
  //  }
  if (ENABLE_CAN)
  {
    twai_general_config_t g_config = TWAI_GENERAL_CONFIG_DEFAULT((gpio_num_t)CAN_TX_PIN, (gpio_num_t)CAN_RX_PIN, TWAI_MODE_NORMAL);  // TWAI_MODE_NORMAL, TWAI_MODE_NO_ACK or TWAI_MODE_LISTEN_ONLY
    twai_timing_config_t t_config  = TWAI_TIMING_CONFIG_250KBITS();
    twai_filter_config_t f_config  = TWAI_FILTER_CONFIG_ACCEPT_ALL();
    twai_driver_install(&g_config, &t_config, &f_config);
    twai_start();
  }
}

/*
   Main loop
*/
void loop()
{
  listenToUsbSerialStream();
  listenToKayoSerialStream();

  //  if (millis() > g_last_can_tx_time + 1000)
  //  {
  //    //sendConveyorWidthToCAN(123);
  //    g_last_can_tx_time = millis();
  //  }
}

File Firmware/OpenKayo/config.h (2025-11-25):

/* ----------------- General config -------------------------------- */
#define  ENABLE_KAYO       true   // Send commands to the target (turn off for experiments / debugging)
#define  REQUIRE_HOMING    true   // Refuse to move until a homing operation has been completed
#define  ENABLE_CAN        false

/* CAN bus */
//#define  CAN_BUS_SPEED         250E3
#define  J1939_UPSTREAM_ADDRESS   0x90   // Range for conveyors: 0x90-9F
#define  J1939_SOURCE_ADDRESS     0x80   // Range for PnP: 0x80-8F, 0xF0-F1 (0xF0-F1 are reserved)
#define  J1939_DOWNSTREAM_ADDRESS 0x91   // Range for conveyors: 0x90-9F
#define  UPSTREAM_LOAD_SPEED       800   // mm/min to run upstream conveyor
#define  DOWNSTREAM_LOAD_SPEED     800   // mm/min to run downstream conveyor


/* Serial */
#define  SERIAL_BAUD_RATE        115200  // Speed for USB serial console
#define  KAYO_BAUD_RATE          115200  // Speed for Kayo serial comms

/* Machine */
#define  KAYO_SCALE_FACTOR      (100.0)  // Multiply mm by this to give Kayo movement units
#define  KAYO_CONVEYOR_CAL        (2.0)  // Calibration adjustment for conveyor width
#define  KAYO_CONVEYOR_CLEARANCE   0.5   // Add this to conveyor width to prevent binding. Set to 0 for calibration.
#define  KAYO_CONVEYOR_OFFSET    565     // The Kayo seems to add this to the value sent
//#define  KAYO_TRACK_MIN_WIDTH    (57.5)
//#define  KAYO_TRACK_MAX_WIDTH   (300.0)
#define  KAYO_ROTATION_SCALE    (3200.0 / 360.0)
//#define  KAYO_X_MAX              (800.0)
//#define  KAYO_Y_MAX              (600.0)
//#define  RESPONSE_NOZZLEROTATION    9
#define  KAYO_N1_Z_STEP_BASE        850
#define  KAYO_Z_STEPS_PER_MM        110   // Machine 1
//#define  KAYO_Z_STEPS_PER_MM        220  // Machine 2
#define  COMMAND_DELAY                0   // ms delay after each command

/* Debugging */
#define  DEBUG_CAN               false
#define  DEBUG_KAYO              true   // Report debug messages relating to comms with the Kayo

/*
      self.ROTATION_SCALE_FACTOR = 3200.0 / 360.0    # 3200 steps / 360 degrees
      SMSG_NOZZLEROTATION_RESPONSE = 9
*/
/* ----------------- Hardware-specific config ---------------------- */
/* Kayo Serial */
#define  KAYO_RX_PIN               2 // 43
#define  KAYO_TX_PIN               1 // 44
//
/* I2C */
#define  I2C_SDA_PIN               5
#define  I2C_SCL_PIN               4

/* CAN bus */
#define  CAN_RX_PIN               17
#define  CAN_TX_PIN               16

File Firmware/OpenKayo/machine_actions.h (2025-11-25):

#ifndef H_MACHINEACTIONS
#define H_MACHINEACTIONS

void cmdResetAndHome()
{
  uint8_t message[8]   = {0xEE, 0xBB, 0x05, 0x00, 0x00, 0x02, 0x00, 0x55};
  g_expected_response[0] = 0xAA;
  g_expected_response[1] = 0xFF;
  //g_expected_response[2] = 0x05;
  //g_expected_response[5] = 0x02;
  //g_expected_response[6] = 0x11;
  g_expected_response[7] = 0x55;
#if DEBUG_KAYO
  Serial.print(millis());
  Serial.println("  f: cmdResetAndHome");
#endif
  sendMessageToKayo(message);

  g_position_message[1] = 0x00;
  g_position_message[2] = 0x00;
  g_position_message[3] = 0x00;
  g_position_message[4] = 0x00;
}


/* ******************* BASIC MOVEMENT ***************** */
/*
   Move the gantry to an X/Y location.
   WARNING: The Kayo WILL NOT MOVE X OR Y while any nozzle is extended AT ALL!
   We have to explicitly retract all nozzles before attempting an X/Y movement.
*/

void decodePositionMessage(uint8_t message[])
{
  uint16_t x_byte_0 = message[2];
  uint16_t x_byte_1 = message[3];
  uint16_t x_raw_pos = (x_byte_1 << 8) + x_byte_0;
  float current_x_position = -1 * (x_raw_pos / KAYO_SCALE_FACTOR);

  uint16_t y_byte_0 = message[4];
  uint16_t y_byte_1 = message[5];
  uint16_t y_raw_pos = (y_byte_1 << 8) + y_byte_0;
  float current_y_position = -1 * (y_raw_pos / KAYO_SCALE_FACTOR);
#if DEBUG_KAYO
  Serial.print("Decoded position: ");
  Serial.print(current_x_position);
  Serial.print(",");
  Serial.println(current_y_position);
#endif
  g_x_reported_position = current_x_position;
  g_y_reported_position = current_y_position;
}

void cmdMoveXY(float x, float y, bool suppress_ok_response)
{
#if DEBUG_KAYO
  Serial.print(millis()); Serial.print("    ");
  Serial.println("f: cmdMoveXY()");
  Serial.print("Going to X: ");
  Serial.println(x);
  Serial.print("Going to Y: ");
  Serial.println(y);
#endif
  if (0.0 != g_nozzle_z_position[0])
  {
    cmdMoveZ(1, 0, true);
    //delay(200);
  }
  if (0.0 != g_nozzle_z_position[1])
  {
    cmdMoveZ(2, 0, true);
    //delay(100);
  }
  if (0.0 != g_nozzle_z_position[2])
  {
    cmdMoveZ(3, 0, true);
    //delay(100);
  }
  if (0.0 != g_nozzle_z_position[3])
  {
    cmdMoveZ(4, 0, true);
    //delay(100);
  }

#if DEBUG_KAYO
  Serial.print(millis()); Serial.print("    ");
  Serial.print("Pos message1: ");
#endif
  printKayoMessage(g_position_message);
  if (NULL != x)
  {
    g_x_position = x;
    float kayo_x_requested = -1 * x * KAYO_SCALE_FACTOR;
    uint16_t kayo_x_dest = (int)kayo_x_requested;
    g_position_message[1] = kayo_x_dest >> 8;
    g_position_message[2] = kayo_x_dest & 0xFF;
  }
  if (NULL != y)
  {
    g_y_position = y;
    float kayo_y_requested = -1 * y * KAYO_SCALE_FACTOR;
    uint16_t kayo_y_dest = (int)kayo_y_requested;
    g_position_message[3] = kayo_y_dest >> 8;
    g_position_message[4] = kayo_y_dest & 0xFF;
  }

  //g_position_message[6] = 0x01;
  g_position_message[6] = 0x04;  // The speed that Glen was using for most moves
  //g_position_message[6] = 0x05;  // Let's see if this speed is ok
  //g_position_message[6] = 0x06;
  //g_position_message[6] = 0x07;  // Crazy warp speed. Can make parts move on the nozzle tip.
  // Do we need to set byte 6 for a speed value? We're currently
  // leaving it as 0x00, but Glen's spreadsheet shows different
  // values being sent. Glen's code does this:
  // def Throw(self,XYpos : tuple, nozzleName : str):
  //   self.DoToolToXY( C4d(XYpos), 1 , movetype = 'NORMAL' )
  // def GotoXYAbsPos(self,xy,speed,movetype  ):# take lists of things to move.
  //   b=self.km.makeXYabsMsg(xy,speed,movetype)
  // def makeXYabsMsg(self, xy: tuple , speed: int, movetype='NORMAL'):
  //   b[6] = (self.ABSMOVETYPES[movetype.upper()] << 4) | speed
  // So Glen's code sets speed to 1 (byte 6 = 0x01) for "throw" operations.
  // His spreadsheet also shows speed of 4 for most movements, and 6 for
  // the first movement after loading a board.

  g_expected_response[0] = 0xAA;
  g_expected_response[1] = 0xA1; // OR g_expected_response[1] = 0xEE; Which?
  g_expected_response[2] = 0x00;
  g_expected_response[3] = 0x00;
  g_expected_response[4] = 0x00;
  g_expected_response[5] = 0x00;
  //g_expected_response[6] = 0x00;
  //g_expected_response[2] = g_position_message[2];
  //g_expected_response[3] = g_position_message[1];
  //g_expected_response[4] = g_position_message[4];
  //g_expected_response[5] = g_position_message[3];
  g_expected_response[6] = 0x00;
  g_expected_response[7] = 0x55;
#if DEBUG_KAYO
  Serial.print(millis()); Serial.print("    ");
  Serial.print("Pos message2: ");
  printKayoMessage(g_position_message);
#endif
  sendMessageToKayo(g_position_message, suppress_ok_response, false);
}


/*
   Move the specified nozzle (1-4) to the requested height
   Example:
     CC 04 1D 00 00 00 14 55
     04 1D is position.
     14 is nozzle 1
   Do we need to keep track of Z position? Currently unknown. Moving
   one nozzle causes the other nozzle in the pair to fully retract, so
   we lose track of where they are. This may cause OpenPnP to think a
   nozzle is extended when it's not. This may or may not be a problem.
   Also, we forcibly retract all nozzles before X or Y moves, because
   the Kayo will refuse to move otherwise.
*/
void cmdMoveZ(uint8_t nozzle, float z, bool suppress_ok_response)
{
#if DEBUG_KAYO
  Serial.print(millis());
  Serial.println("  f: cmdMoveZ()");
#endif

  if (-9999.00 == z)
  {
    return;
  }

  uint16_t z_microsteps = KAYO_N1_Z_STEP_BASE + (abs(z) * KAYO_Z_STEPS_PER_MM);

  uint8_t message[8]  = {0xCC, 0x00, 0x00, 0x00, 0x00, 0x00, 0x04, 0x55};  // Byte 6 sets speed to 4
  message[1] = z_microsteps >> 8;
  message[2] = z_microsteps & 0xFF;
  if (0 == z)
  {
#if DEBUG_KAYO
    Serial.println("Special-casing zero position");
#endif
    message[1] = 0x00;
    message[2] = 0x00;
  }

  switch (nozzle)
  {
    case 1:
      g_nozzle_z_position[0] = z;
      g_nozzle_z_position[1] = 0.0;  // Nozzles 1 and 2 are ganged
      message[6] = 0x14;
      break;
    case 2:
      g_nozzle_z_position[0] = 0.0;  // Nozzles 1 and 2 are ganged
      g_nozzle_z_position[1] = z;
      message[6] = 0x24;
      break;
    case 3:
      g_nozzle_z_position[2] = z;
      g_nozzle_z_position[3] = 0.0;  // Nozzles 3 and 4 are ganged
      message[6] = 0x34;
      break;
    case 4:
      g_nozzle_z_position[2] = 0.0;  // Nozzles 3 and 4 are ganged
      g_nozzle_z_position[3] = z;
      message[6] = 0x44;
      break;
  }

  g_expected_response[0] = 0xAA;
  g_expected_response[1] = 0xA2;
  g_expected_response[2] = message[2];
  g_expected_response[3] = message[1];
  g_expected_response[6] = nozzle;
  g_expected_response[7] = 0x55;

  sendMessageToKayo(message, suppress_ok_response);
#if DEBUG_KAYO
  Serial.println("z sent");
#endif
}


/*
  Diagnostic function to send a specific number of microsteps to a
  nozzle Z axis stepper.
*/
void cmdSendZSteps(uint8_t nozzle, uint16_t z_microsteps)
{
  if (-9999 == z_microsteps)
  {
    z_microsteps = 0;
  }
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

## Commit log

2022-12-29 Added config option to enable message debugging. Track both requested X/Y position and reported position. Added ability to require exact match on expected response messages. Added config option to ap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
2022-12-30 Expanded axes to allow control of 4 nozzles via GCode. Special-case on moving to 0 on Z axes to allow true full retraction.
2022-12-30 Added message formats from Glen's Python driver for reference.
2023-07-21 Fixed handling of blowoff by controlling suppliment valve.
    [OpenKayo.ino, gcode.h, machine_actions.h]
2023-07-21 Turned on require-homing in default config and clarified other config values.
2023-12-16 Pin changes to support dedicated OpenKayo hardware.
2025-11-25 Firmware conversion to S3, with CAN bus currently partly broken.
    [OpenKayo.ino, can_comms.h, config.h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]
2025-11-25 Added hardware design files and updated README.
    [OPENKAYO-v1_1.brd, OPENKAYO-v1_1.sch]
2025-11-25 Expanded README with documentation of G-Codes, axes, and camera connections.
2025-11-26 Added printable parts to assist with conversion
    [Discard Tray Gridfinity 1x1 z=3.5.f3d, Discard Tray Gridfinity 1x1 z=3.5.stl, Discard Tray Holder Gridfinity.f3d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]
2025-11-30 Added images and instructions for mounting ELP camera
